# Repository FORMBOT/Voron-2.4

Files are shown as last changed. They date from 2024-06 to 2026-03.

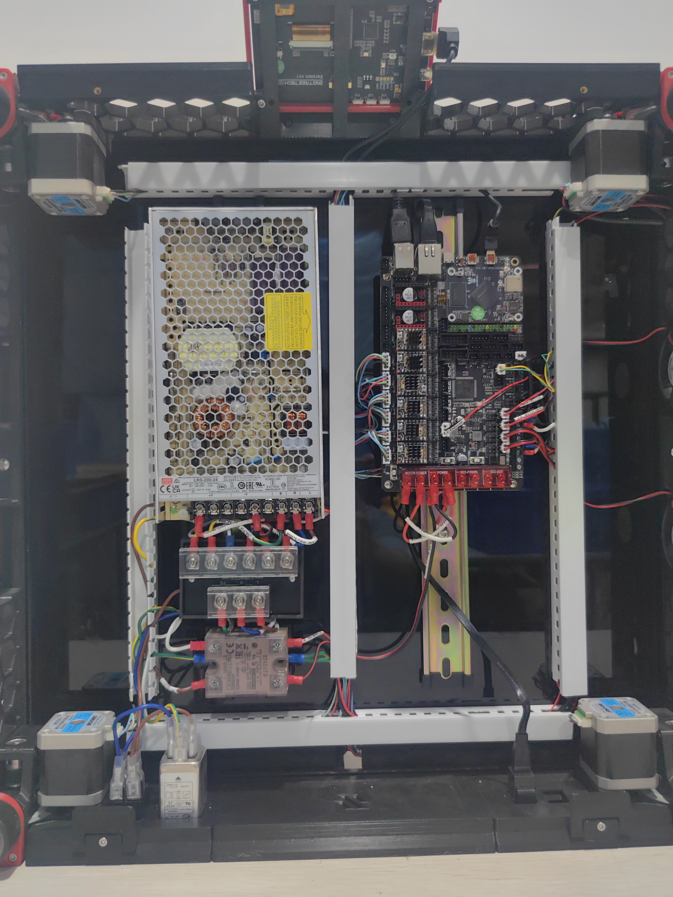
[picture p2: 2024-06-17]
Diagrams/Wiring Overview of V2.4 R2 Pro+.jpg

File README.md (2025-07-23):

# Voron V2.4 Formbot Kit

[Kit Website](https://www.formbot3d.com/products/voron-24-r2-pro-corexy-3d-printer-kit-with-m8p-cb1-board-and-canbus-wiring-system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)

# Overview

* [Build Notes](https://github.com/FORMBOT/Voron-2.4/tree/main/Build%20Notes)
* [Firmware Flashing](https://github.com/FORMBOT/Voron-2.4/tree/main/Firmware%20Flashing)
* [Config Setup and Initial Startup](https://github.com/FORMBOT/Voron-2.4/tree/main/Config)
* Maintenance
* [All STLs](https://github.com/FORMBOT/Voron-2.4/tree/main/STL)
* only custom STLs
* Printer Tuning
* Printer Testing

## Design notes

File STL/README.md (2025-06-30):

# Notes
STLs are tried to be kept up to date.
Original Repos: 
https://github.com/VoronDesign/Voron-2
https://github.com/VoronDesign/Voron-Stealthburner
https://github.com/VoronDesign/Voron-Tap
https://github.com/bigtreetech/EBB/tree/master/EBB%20SB2209%20CAN%20(RP2040)
https://github.com/nevermore3d/Nevermore_Micro/tree/master/V5_Duo
and some specific parts ;)

# Filename Nomenclature

| Filename | Note |
|---|---|
| \*.stl | Base color |
| [a]\_\*.stl | Accent color |
| [o]\_\*.stl | Opaque (light doesn't penetrate) |
| [c]\_\*.stl | Clear/Translucent (light can penetrate) |

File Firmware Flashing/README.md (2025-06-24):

# Firmware Flashing

First of all, be sure that your wiring is **100% correct** before you first power on your Printer. You should **disconnect* the bed heater and the SB2209 RP2040 completely, otherwise they may heat which could destroy your printed parts, hotend, bed heater, magnet sheet or thermal fuse.

## CB1/CB2 Setup
*this guide translates 1:1 to BTT Pi v1.1 / v2*
1. Get the [latest release of the cb1 firmware](https://github.com/bigtreetech/CB1/releases) (for cb2 get the [latest cb2 firmware release](https://github.com/bigtreetech/CB2/releases)). You want to download the XXX...XXX.img.xy file. This may take some time.
2. While you are waiting for the file to download, install the [Raspberry Pi Imager](https://www.raspberrypi.com/software/).
3. Unpack the firmware so you have a .img file.
4. Open the Raspberry Pi Imager, click on Choose OS, scroll down to the very end, klick on "Use Custom" and select the .img file you just unpacked.
5. Select the MicroSD card with the "Choose Storage" function.
6. Click on "WRITE" and accept that all previous data on the SD card will be deleted.
7. If the imager didn't already eject the SD-Card, eject it, pull it out from your Computer and plug it back in.
8. The Card will now show up as "BOOT".
9. Open the system.cfg file.
10. Remove the `#` in front of hostname and change it to whatever name you want your printer to show up in your network. E.g. `hostname="Voron"`
11. Remove the `#` in front of TimeZone and change it to your local time zone, E.g. `Europe/Munich`, `America/New_York` or `Asia/Shenzen`.
12. Go to WIFI_SSID and change it to your Wifi Name (`WIFI_SSID="YOURWIFINAME"`).
13. Go to WIFI_PASSWD and change it to your Wifi Password (`WIFI_PASSWD="YOURWIFIPASSWORD"`).
14. **DONT EDIT ANYTHING ELSE UNLESS YOU KNOW EXACTLY WHAT YOU ARE DOING!**

## CM4/5 Setup
*this guide translates 1:1 to Raspberry Pi 4 / 5*
1. Download and install [Raspberry Pi Imager](https://www.raspberrypi.com/software/).
2. Click “Choose OS” and scroll down to “Other specific-purpose OS”.
3. Select “3D Printing” and choose “Mainsail OS”.
4. Choose your SD Card.
5. If you will be using Wi-Fi, click on the GEAR icon in the bottom right corner and enter your Wi-Fi information.
6. Click on “SAVE” and on “WRITE”. and accept that all previous data on the SD card will be deleted.
7. Make sure that your MCU(s) is connected to your pi. If you will be using wired networking, also make sure your ethernet cable is connected.
8. Insert the microSD card into your Pi, and power on the Pi.
9. Find your Pi on the network, and ssh into it (using PuTTY on Windows or the terminal on MacOS). The default username is pi and the password is raspberry.
	* If your network supports bonjour, the pi should show up as mainsailos.local
	* If your network automatically assigns DNS hostnames, it may simply show up as mainsailos
	* Failing these two options, you may need to check your router’s DHCP server, and find out what IP address as been assigned to the device.

## CANBUS Setup
1. First of all, take a look at the [CANbus basics](https://canbus.esoterical.online).
2. Now [set up the CANbus Network](https://canbus.esoterical.online/Getting_Started.html).
3. [Flash your Mainboard](https://canbus.esoterical.online/mainboard_flashing.html). You need to flash it in USB-CAN-Bridge. You can find the needed Mainboard settings / hardware [here](https://canbus.esoterical.online/mainboard_flashing/common_hardware/BigTreeTech%20Manta%20M8P%20v2.0/README.html).
4. Now [flash your SB2209 RP2040](https://canbus.esoterical.online/toolhead_flashing.html). You can find the needed settings / hardware [here](https://canbus.esoterical.online/toolhead_flashing/common_hardware/BigTreeTech%20SB2209%20(RP2040)/README.html).
5. Note your UUIDs and note which one is the one of the Mainboard and which belongs to the toolhead.

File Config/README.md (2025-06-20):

# Configuration & Basic Macros

You still need to adjust a few things which are depending on your printer size!

Go through the config carefully. Everyone is responsible for their own configuration and for any damage that may occur due to incorrect configuration. "Uncomment" means remove the "#" in front of the line.

After you completed the first steps of your configuration, follow the [Voron Initial Startup Guide](https://docs.vorondesign.com/build/startup/) to set up everything else and be sure it works correct.
Follow [slicer setup](https://docs.vorondesign.com/build/slicer/) to set up your slicer.

Now that everything is set up, it's time for the [secondary Printer tuning](https://docs.vorondesign.com/tuning/secondary_printer_tuning.html) so your first print won't be a complete disaster.

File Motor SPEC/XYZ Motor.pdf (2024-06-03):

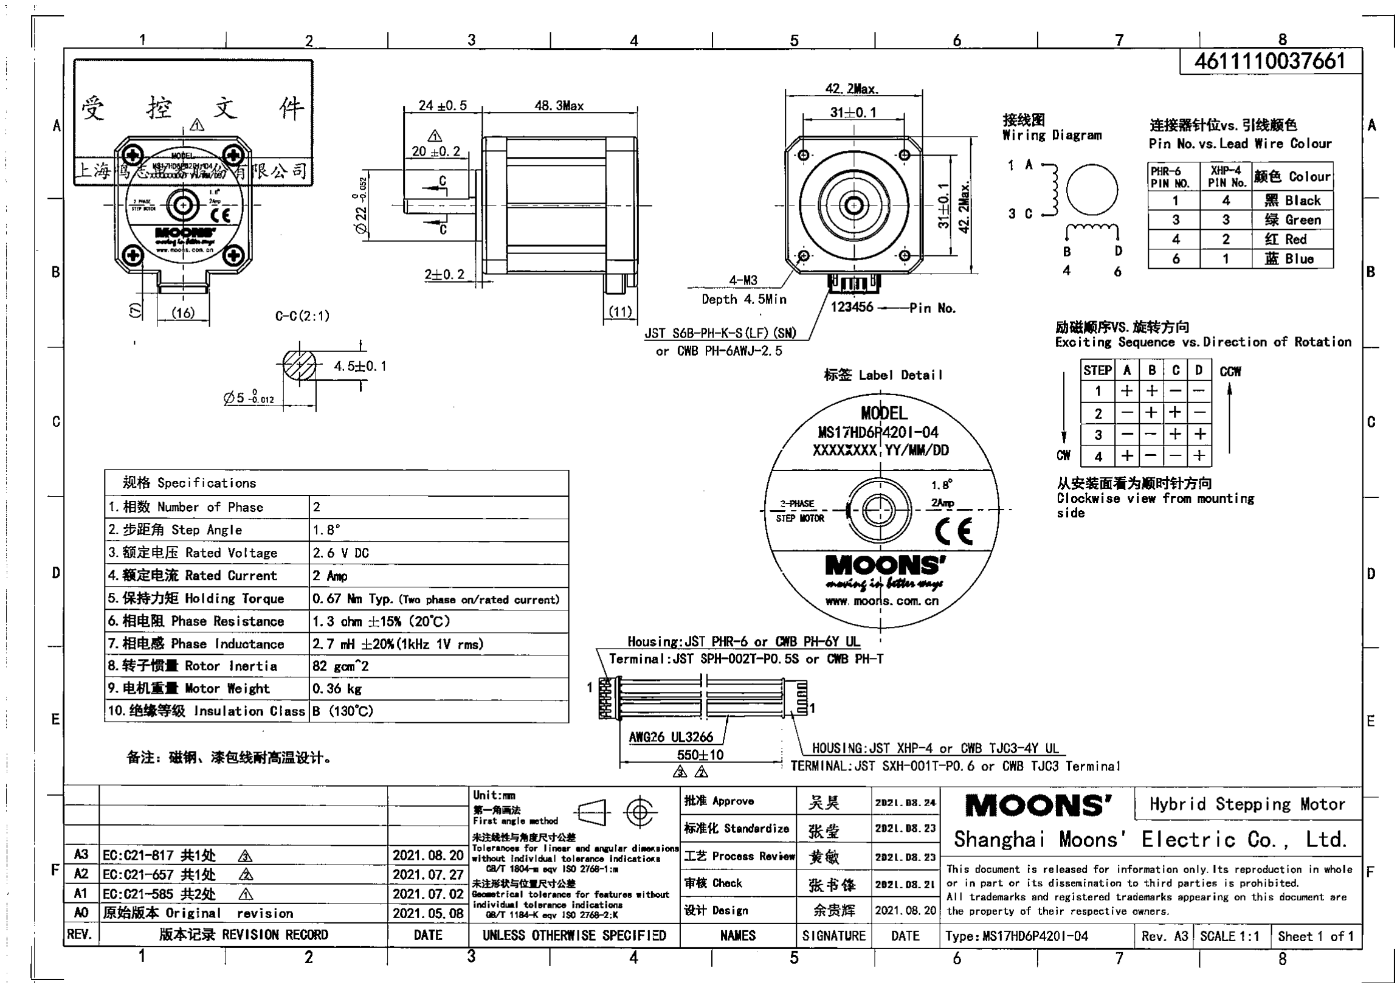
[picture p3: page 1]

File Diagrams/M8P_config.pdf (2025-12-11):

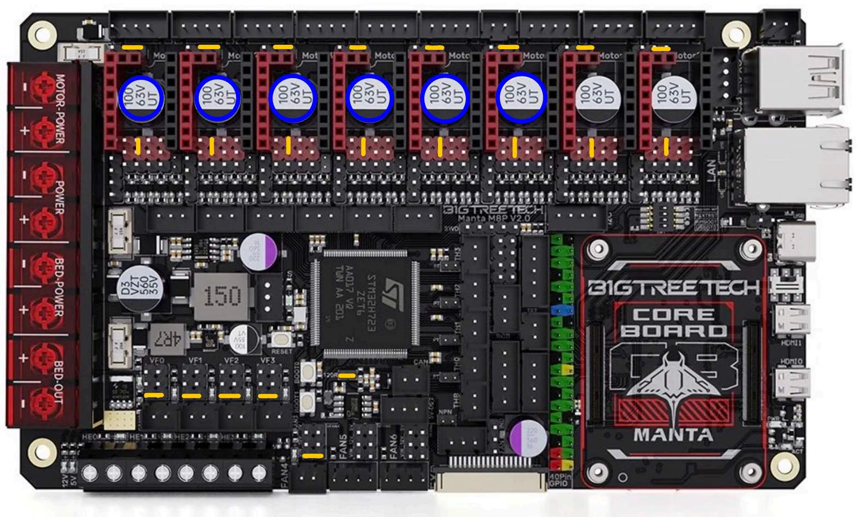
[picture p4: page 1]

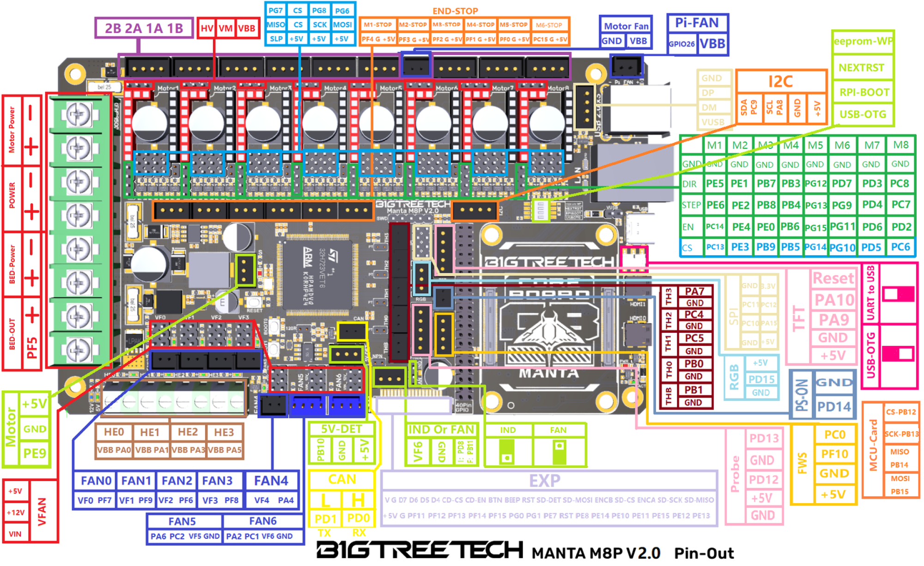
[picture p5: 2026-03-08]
Diagrams/Pins/BIGTREETECH MANTA M8P V2-0 PinOut.png

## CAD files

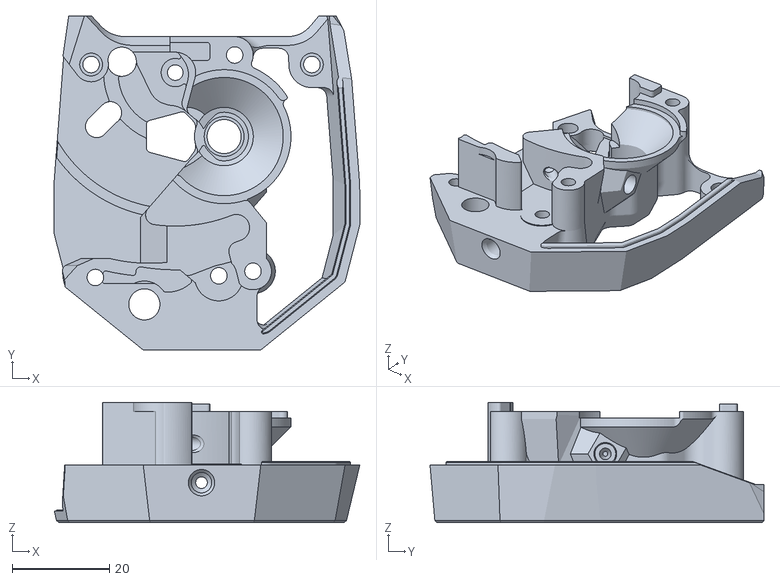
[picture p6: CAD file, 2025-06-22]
STL/Stealthburner/Clockwork2/Direct_Drive/main_body.stl
62.8 x 68.7 x 24.7

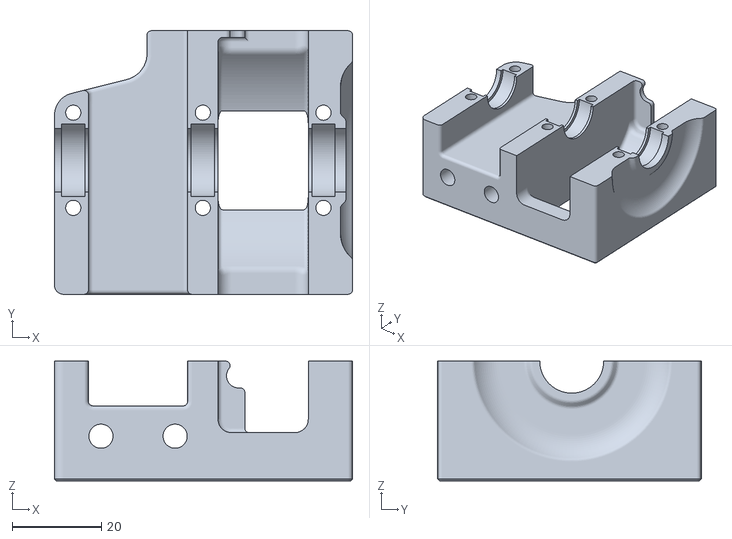
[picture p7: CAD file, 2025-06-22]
STL/Z_Drive/z_drive_main_a_x2.stl
66.7 x 59.0 x 26.8

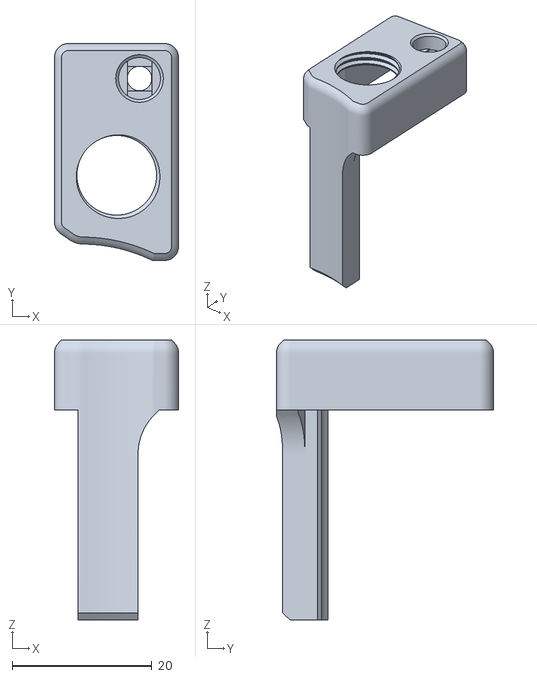
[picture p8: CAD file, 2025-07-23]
only custom STLs/Accent/PG7 Gantry Adapter.stl
17.7 x 31.0 x 40.0

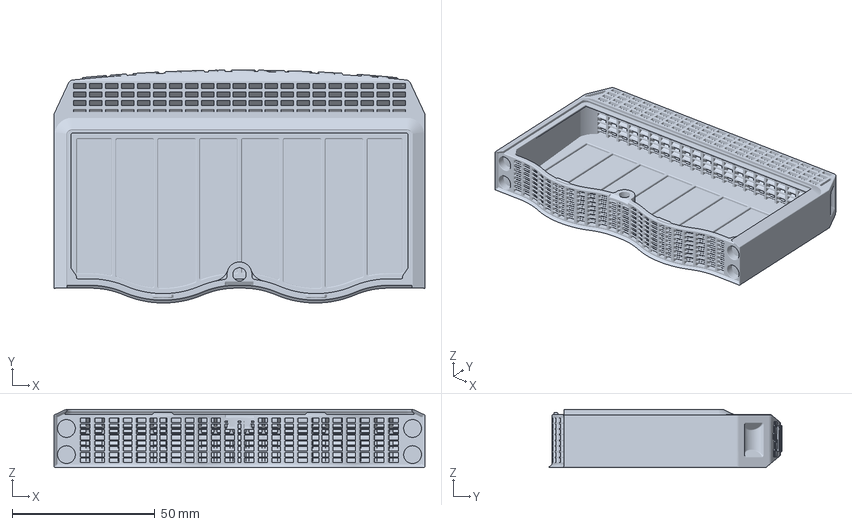
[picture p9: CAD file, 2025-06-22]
only custom STLs/Nevermore/XL_Cartridge(contributed_by_Bucknova).3mf
130.0 x 81.6 x 20.5 mm

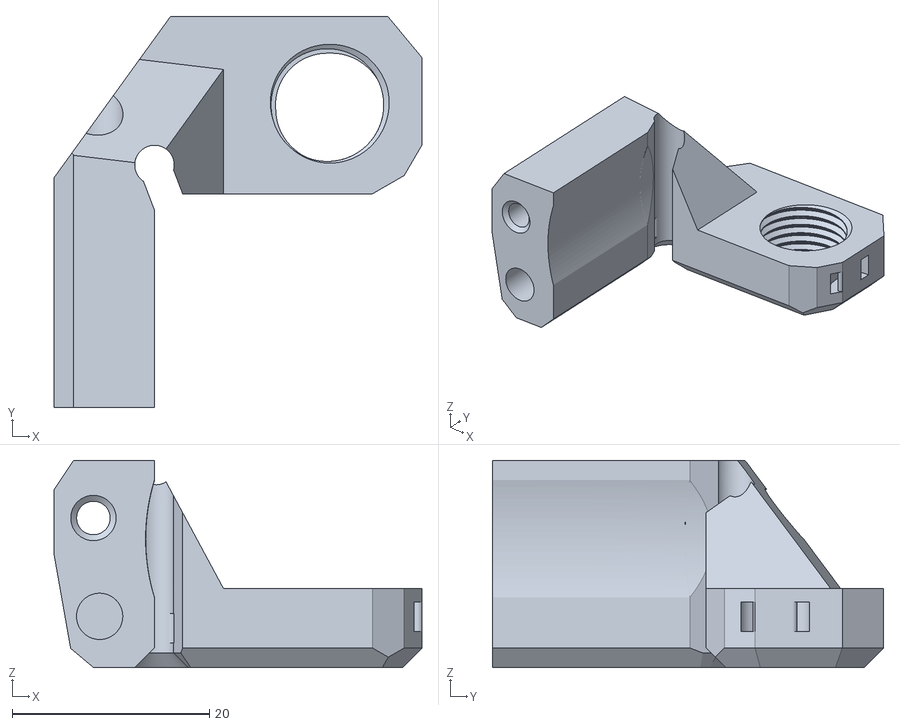
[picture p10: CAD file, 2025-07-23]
only custom STLs/Primary/Anchor v2.stl
37.3 x 39.7 x 21.1

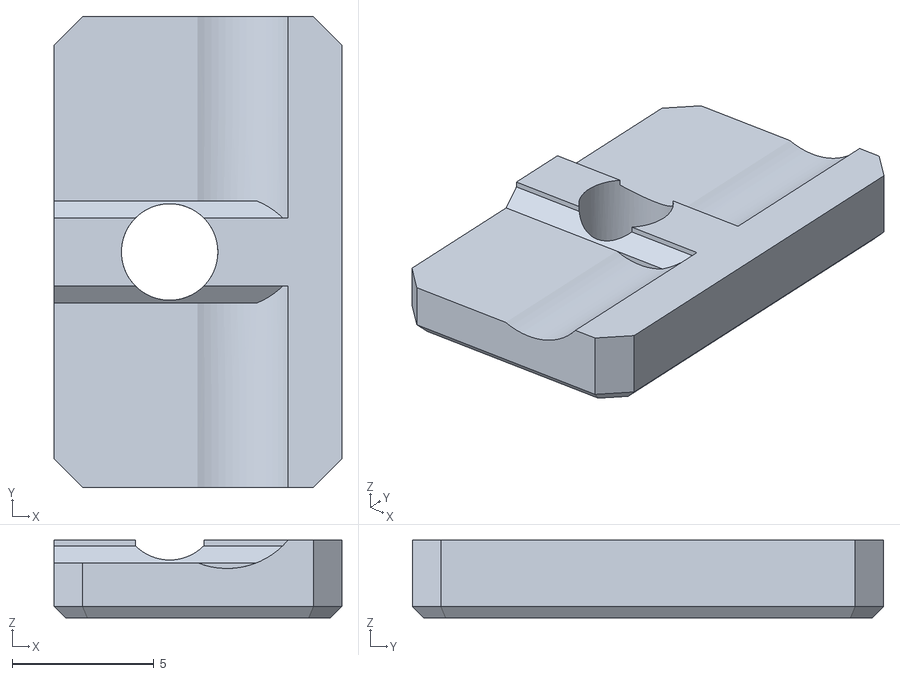
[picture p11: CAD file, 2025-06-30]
only custom STLs/Tap/[a]_Tap_Belt_Cover_r8_x2.stl
10.1 x 16.6 x 2.74

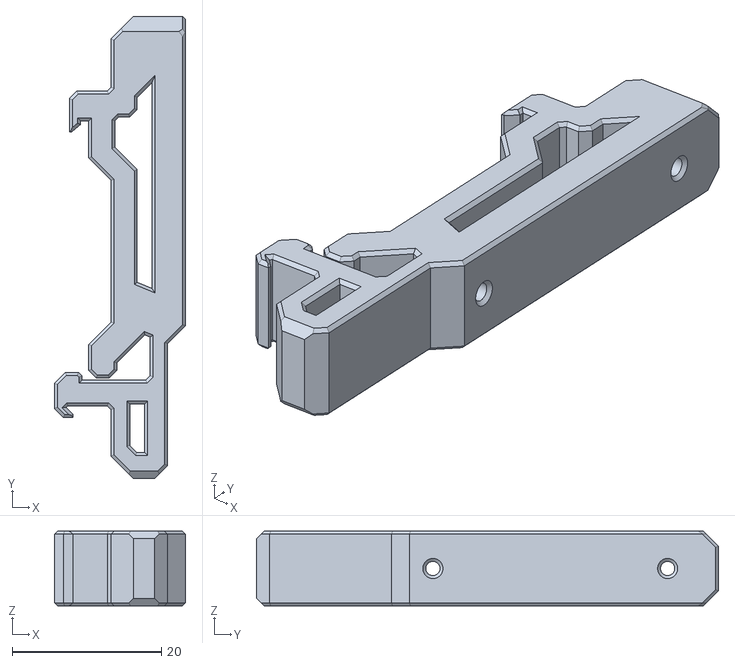
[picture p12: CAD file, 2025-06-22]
STL/Electronics_Bay/pcb_din_clip_x2.stl
17.6 x 62.0 x 10.0

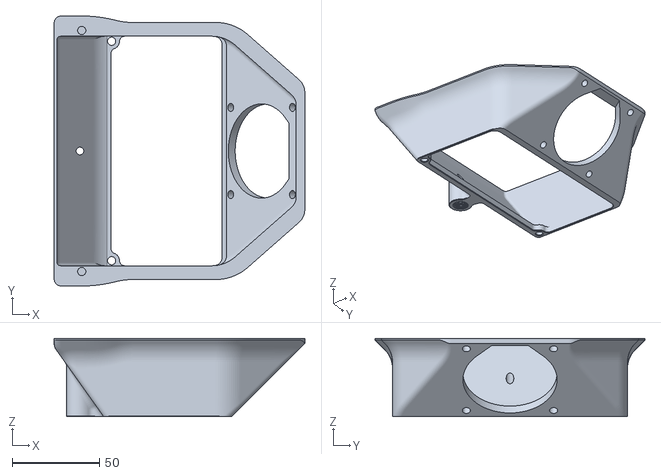
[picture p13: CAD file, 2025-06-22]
STL/Exhaust_Filter/exhaust_filter_housing.stl
143.7 x 154.8 x 45.0

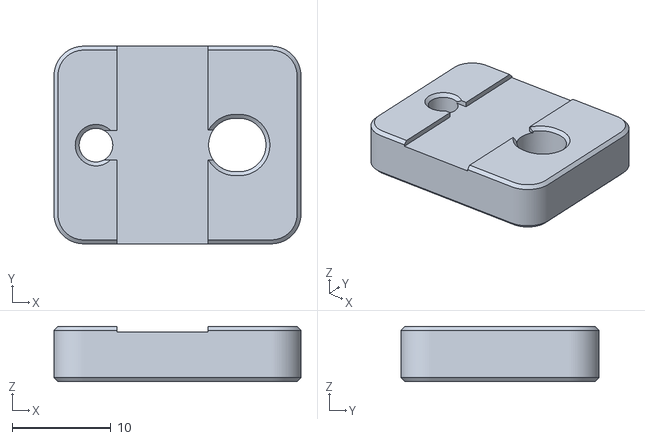
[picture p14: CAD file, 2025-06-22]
STL/Gantry/[a]_z_belt_clip_lower_x4.stl
25.0 x 20.0 x 5.60

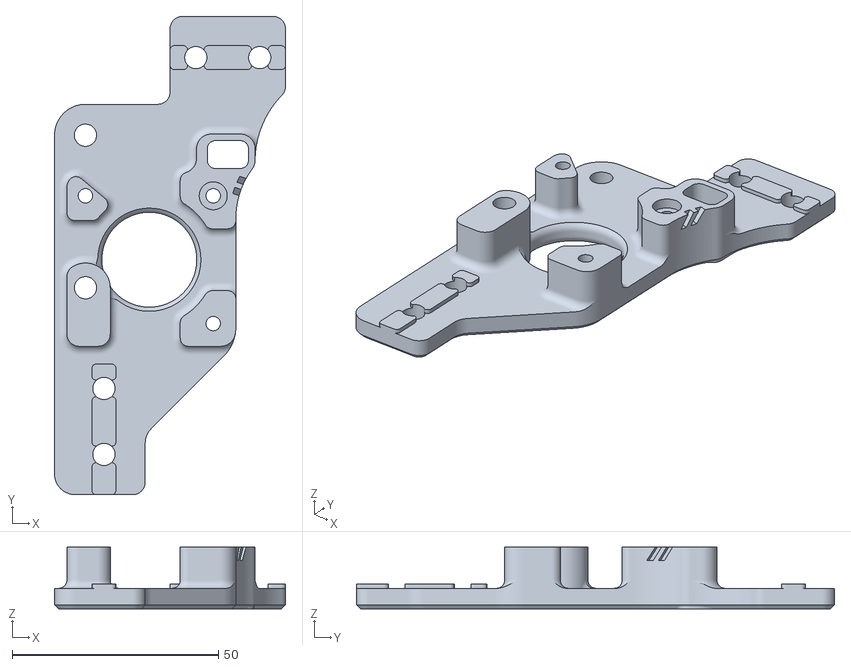
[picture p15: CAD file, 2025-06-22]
STL/Gantry/AB_Drive_Units/b_drive_frame_upper.stl
56.0 x 116.0 x 15.0

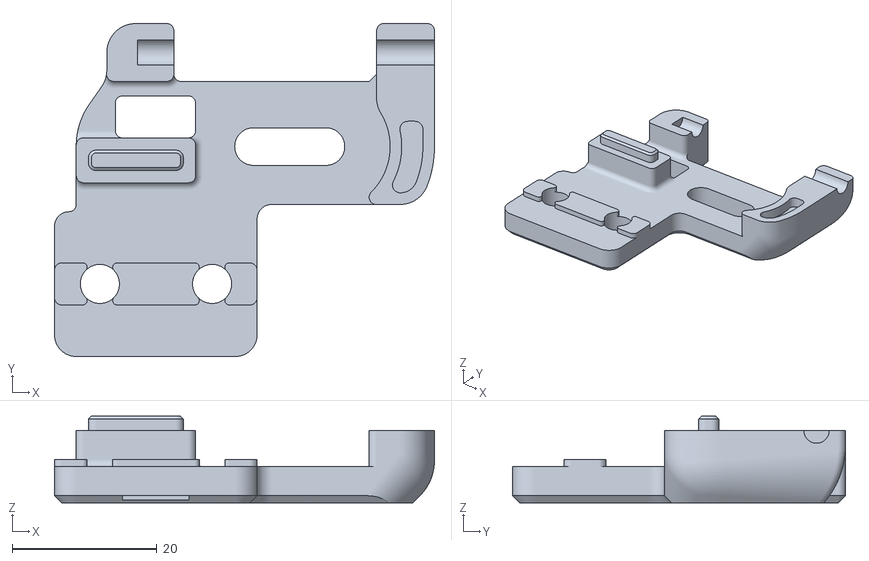
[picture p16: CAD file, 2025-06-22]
STL/Gantry/Front_Idlers/front_idler_right_upper.stl
52.5 x 46.0 x 12.0

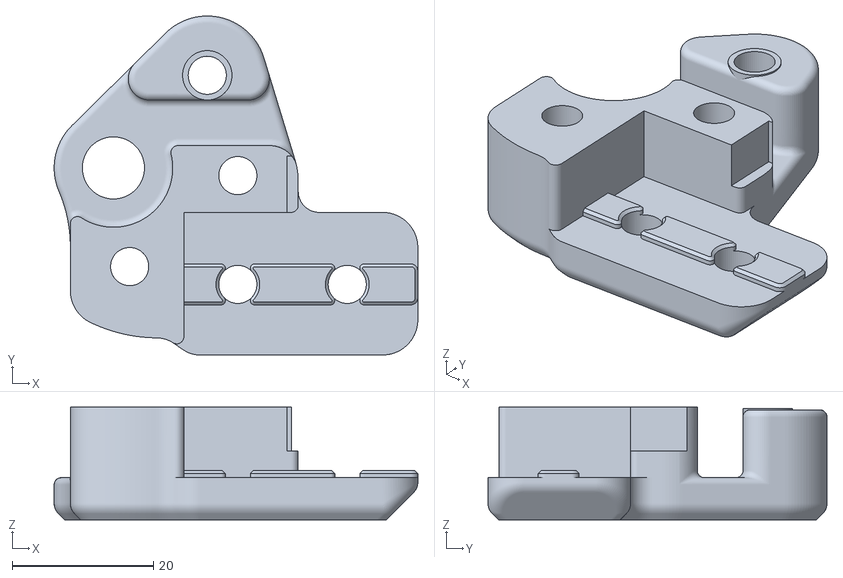
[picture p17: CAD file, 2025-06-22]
STL/Gantry/XY_Joints/xy_joint_left_upper_MGN12.stl
51.5 x 48.0 x 16.0

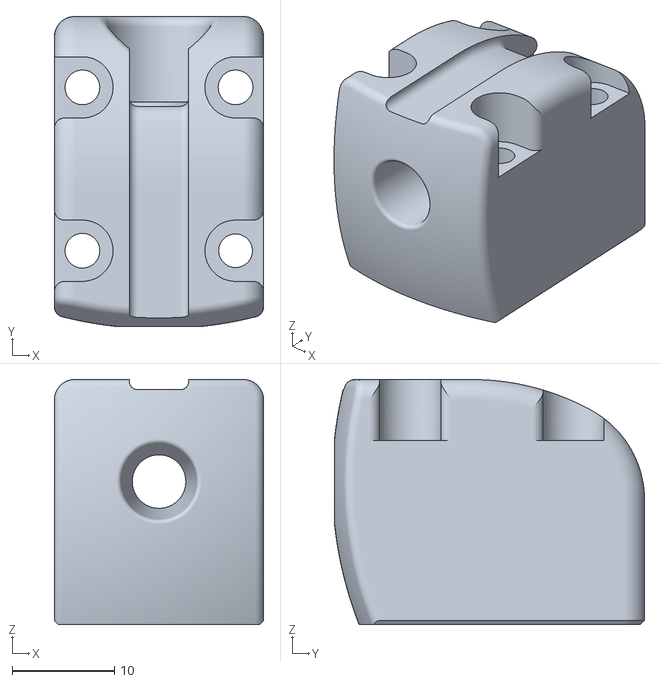
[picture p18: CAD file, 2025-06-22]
STL/Gantry/Z_Joints/z_joint_lower_x4.stl
20.5 x 30.4 x 24.0

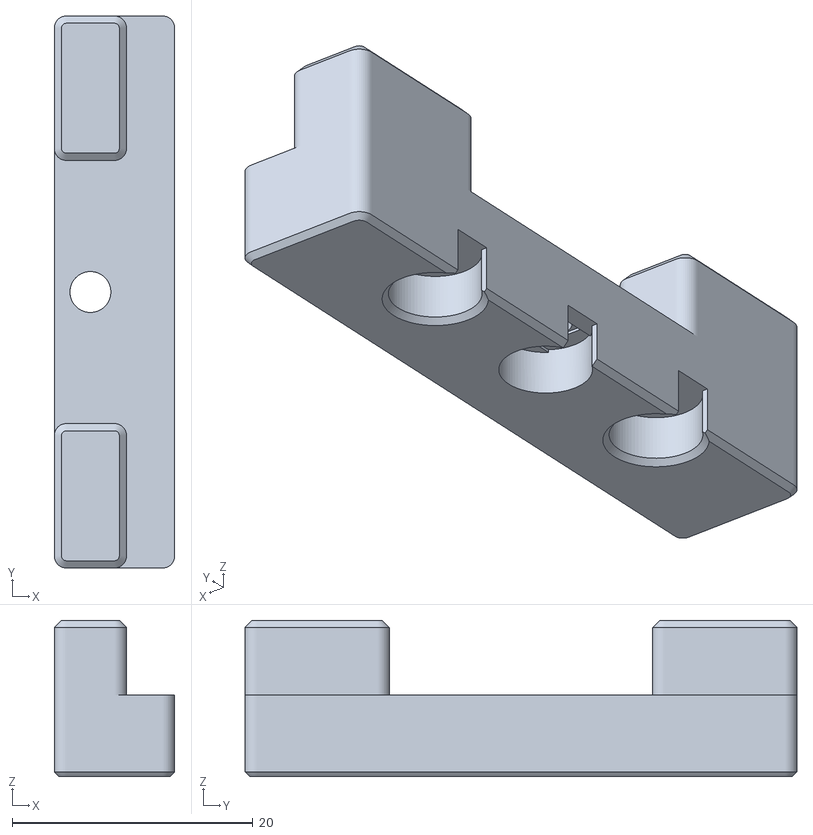
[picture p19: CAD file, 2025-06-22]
STL/Panel_Mounting/Front_Doors/latch_x2.stl
10.0 x 45.9 x 13.0

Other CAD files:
STL/Z_Drive/z_drive_main_b_x2.stl
STL/Panel_Mounting/midspan_panel_clip_6mm_x8.stl
STL/Skirts/250/front_skirt_a_250.stl
STL/Skirts/300/rear_center_skirt_300.stl
STL/Electronics_Bay/Manta-M8P_Bracket.stl
STL/Electronics_Bay/PSU_stabilizer_50mm.stl
STL/Electronics_Bay/lrs_200_psu_bracket_x2.stl
STL/Exhaust_Filter/[a]_exhaust_fan_grill.stl
STL/Exhaust_Filter/[a]_exhaust_filter_mount_x2.stl
STL/Exhaust_Filter/[a]_filter_access_cover.stl
STL/Exhaust_Filter/exhaust_filter_grill.stl
STL/Gantry/AB_Drive_Units/[a]_PG7-Umbilical Motor Mount.stl
STL/Gantry/AB_Drive_Units/[a]_z_chain_retainer_bracket_x2.stl
STL/Gantry/AB_Drive_Units/a_drive_frame_lower.stl
STL/Gantry/AB_Drive_Units/b_drive_frame_lower.stl
STL/Gantry/Front_Idlers/[a]_tensioner_left.stl
STL/Gantry/Front_Idlers/[a]_tensioner_right.stl
STL/Gantry/Front_Idlers/front_idler_left_lower.stl
STL/Gantry/Front_Idlers/front_idler_left_upper.stl
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

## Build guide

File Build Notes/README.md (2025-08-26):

# Functional parts build notes (to get the Printer up and running)
Start with the [Stock Voron 2.4 Manual](https://github.com/VoronDesign/Voron-2/tree/Voron2.4/Manual).
Be aware that the v2.4 Manual uses a 250mm Version of the v2, so some dimensions may seem wrong if you build a 300mm/350mm Version.

## P. 25 v2.4 manual: 
If you build a bigger Version than a 250mm, you need more screws / m3-T-Nuts. Start from the outer holes in the rail and work your way towards the middle screwing the rail down every second hole.
The carriages are designed to slide along the rail easily. This unfortunately also includes sliding off the rails. Dropping the carriage likely irreparably damages it. ALWAYS put the little black rubber Carriage stoppers back on the rail (into the holes without screws) until your printer ist up and runnning!

## P. 29 v2.4 manual:
The DIN-Rails need to be rotated 90 Degrees so the cables are long enough later. They should run parallel to the bed extrusions (from front to back).

## P. 84 v2.4 manual: 
Skip this step, this part is not used and therefore probably not included in your printed parts.

## P. 88 v2.4 manual: 
If you are building a 300mm machine you will need to start you screws from the second screw hole in the rails leaving the end holes open to allow space for T-nuts at later steps.
Small reminder: The carriages are designed to slide along the rail easily. This unfortunately also includes sliding off the rails. Dropping the carriage likely irreparably damages it. ALWAYS put the little black rubber Carriage stoppers back on the rail (into the holes without screws) until your printer ist up and runnning!

## P. 101 v2.4 manual: 
Again, if you are building a bigger printer than the 250mm version, start at the outer holes and screw the rail down every second hole.
Small reminder (again): The carriages are designed to slide along the rail easily. This unfortunately also includes sliding off the rails. Dropping the carriage likely irreparably damages it. ALWAYS put the little black rubber Carriage stoppers back on the rail (into the holes without screws) until your printer ist up and runnning!

## P. 104 v2.4 manual: 
As said before, the part on top of the right XY-Joint is not used with this kit. Use m5x10 BHCS like on the left XY-Joint to secure the X Axis to the XY-Joints.

## P. 122 v2.4 manual: 
After you installed the Z-belts and squared the Gantry, make sure your AB belts are exactly the same length and have the exact same amount of teeth! Proceed with routing the AB-Belts, but be Aware that you will use a different X carriage as in the Voron 2.4 Manual.

## P. 129-131 v2.4 manual: 
Skip these pages. Put the AB belts to the MGN12 Carriage with some tape, they dont have to be tight.

## P. 143 v2.4 manual: 
X Carriage: After finishing the AB-Belts Routing, switch to the [TAP Manual](https://github.com/VoronDesign/Voron-Tap/tree/main/Manual). Optotap is used as the sensor.
Be sure to take a look into the R8_errata.md document, it Highlights some important changes from the Manual and install the X Endstop switch.

## P. 33 Tap Manual: 
After you have installed Tap successfully and have the AB belts fixed in the tap carriage, switch to page 146 of the Voron 2.4 manual or to the [Stealthburner manual](https://github.com/VoronDesign/Voron-Stealthburner/tree/main/Manual).
We will come back to install the Toolhead later.

## P. 13 Stealthburner manual: 
You use a Toolhead PCB, so install these two heat inserts.

## P. 14 Stealthburner manual: 
Skip

## P. 30 Stealthburner manual: 
Follow [this Video Guide](https://www.youtube.com/watch?v=ly22qmB3NxE&t=1s) on how to set the gear mesh on your CW2.
Follow [this video Guide](https://www.youtube.com/watch?v=L1gxBCiE0pk) on how to set the Anti-Squish as well.

## P. 31 Stealthburner manual: 
Skip for now, we will install our Version of the Anchor later.

## P. 34 Stealthburner manual: 
You dont need to fix the Cable Cover down with the m3x6 BHCS now, you will need to access this later.

## P. 36-43 Stealthburner manual: 
All Hotends are mounted in a similar pattern and pretty self-explaining, your hotend mount and hotend will look different.

## P. 46-51 Stealthburner manual: 
Be very careful with the cables, you can easily rip them off the LED PCB which leads to this LED and the following ones not working.

## P. 53 Stealthburner manual: 
Be sure that your fan blows in the right Direction. Look at the arrows on the fan. Additionally, the Sticker on the fan is on the back pointing towards the Hotend. You want the fan to blow air into the hotend, not trying to pull the air out. This destroys your fan and your whole hotend mount because of heatcreep.

## P. 56 Stealthburner manual: 
You dont need to screw the 5015 fan into the SB Face, you will install the SB0000 Fan PCB there later.

## P. 58 Stealthburner manual: 
All parts of the Stealthburner are now pretty much finished. Now you will need to install the Can-Board on there and do some basic wiring. Switch to the [SB2209 RP2040 Manual](https://github.com/bigtreetech/EBB/tree/master/EBB%20SB2209%20CAN%20(RP2040)/Build%20Guide).

## P. 02 SB2209 manual: 
Now you need to screw down the 5015 fan with the SB0000 PCB :)

## P. 03/04 SB2209 manual: 
You need to select Vin (24V) for all fans. Be sure to wire Gnd to Gnd and 24V to 24V! Otherwise you will experience magic smoke later.

## P. 05 SB2209 manual: 
Skip

## P. 06 SB2209 manual: 
Be sure to wire Gnd to Gnd, Signal to Signal and 24V to 24V! Otherwise you will experience magic smoke later.

## P. 13 SB2209 manual: 
You Need to set the switch to 1: on; 2: on; 3: off; 4: on

## P. 15 SB2209 manual: 
Skip

## P. 16 SB2209 manual:
Be sure to use the endstop labeled "To CAN_Endstop" which is the one with the short wires.

## P. 18 SB2209 manual: 
Skip

## P. 19 SB2209 manual: 
Skip, Stealthburner will be assembled later.

## P. 24 SB2209 manual: 
You will need to Strip down the Isolation a bit so you have enough cable length to connect the cable to the PSU and to the Can port. Go back to the Tap Manual page 34 now, flashing the toolhead will be done later.
Use the tight cable sleeve around the cable.

## P. 36 Tap manual: 
Stealthburner and Tap are now completed and installed. Switch back to p. 148 of the original V2.4 manual.

## P. 149 v2.4 manual:
Rotate the din rails 90° compared to the original layout.

## P. 150-152 v2.4 manual: 
Skip; Raspberry Pi mounting and 5v PSU mounting is not needed. Instead, mount the CB1 / CM4 on the Manta.

## P.158-164 v2.4 manual:
Skip; TAP is your Z-Endstop, your X Endstop sits on Tap and your Y endstop will be mounted on the A Motor mount later.

## P. 165 v2.4 manual: 
You use the 3in6 Power Distributor instead.

## P. 170 v2.4 manual:
small reminder, you dont use a Raspberry Pi.

## P. 172 v2.4 manual:
another small reminder, you don't use a 5v PSU.

## P. 175-178 v2.4 manual:
Skip these steps, instead configure your Manta like this:
M8P_v2 Jumper / Driver marking
Place a Jumper on all yellow marked pins and place the TMC2209s with attached heatsink on all driver ports with a blue circle after installing the jumpers.

## P. 183 v2.4 manual: 
Leave the cables to the 5v PSU out.

## P. 184 v2.4 manual:
The Z-Endstop cables are not needed.

## P. 185 v2.4 manual: 
Be **100%** sure that the SSR cables are connected correctly, **otherwise your printer is _not_ safe to be powered on**.

## P. 186-189 v2.4 manual:
This kit doesn't use Wagos to distribute the High Voltage cables.

## P. 190-193 v2.4 manual: 
These steps are for an octopus Mainboard. Use this wiring diagram instead: v2.4 M8P wiring diagram
For now, only connect z0-z3, the bed heater, 24V from the 24V PSU and the bed thermistor.

## P. 194-199 v2.4 manual:
Skip these steps, you use Umbilical on X and Y.

## P. 204 v2.4 manual:
You use a bit different Wire guide where you have to screw in a pg7 cable gland. From here you route the Can cable down through the z chain, together with the A and B Motor cables. 
v2.4 M8P wiring diagram 
Connect the B motor (left motor) to X Motor, connect the A motor (right motor) to Y Motor.
Connect the CAN-Cable to the right CAN-Port on the M8P and 24V / GND to the 24V PSU. If you think the cables are not Long enough, you haven't done [this step](https://github.com/FORMBOT/Voron-2.4/tree/main/Build%20Notes#p-24-sb2209-manual).

# Cosmetic parts build notes (not needed to get the pinter running)

## P. 206-209 v2.4 manual:
You can skip these steps.

## P. 211 & 214-216 & 220-221 v2.4 manual:
Skip; you don't need these parts because you use the touchscreen.

## P. 231 v2.4 manual:
Use the v2.4 M8P wiring diagram to wire the electronics fans.

## P. 233 v2.4 manual: 
Don't close the electronics compartment yet, you will need to acces this while flashing the boards.

## P. 256 v2.4 manual:
Use the big cable sleeve around the exhaust fan cable (if you use the stock exhaust).

# Don't power on the printer if you are not 100% sure you wired everything correct!
And have a look into [this](https://github.com/FORMBOT/Voron-2.4/blob/main/Diagrams/Instruction%20of%20V2.4%20R2%20Pro%2B.pdf).

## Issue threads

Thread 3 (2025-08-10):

published config has broken [resonance_tester] block

shiftingtech, 2025-08-10:
published config contains a [resonance_tester] block ,but not the required `accelerometer` line  (plus the entire [adxl3465] block is missing), resulting in a nonfunctional config.

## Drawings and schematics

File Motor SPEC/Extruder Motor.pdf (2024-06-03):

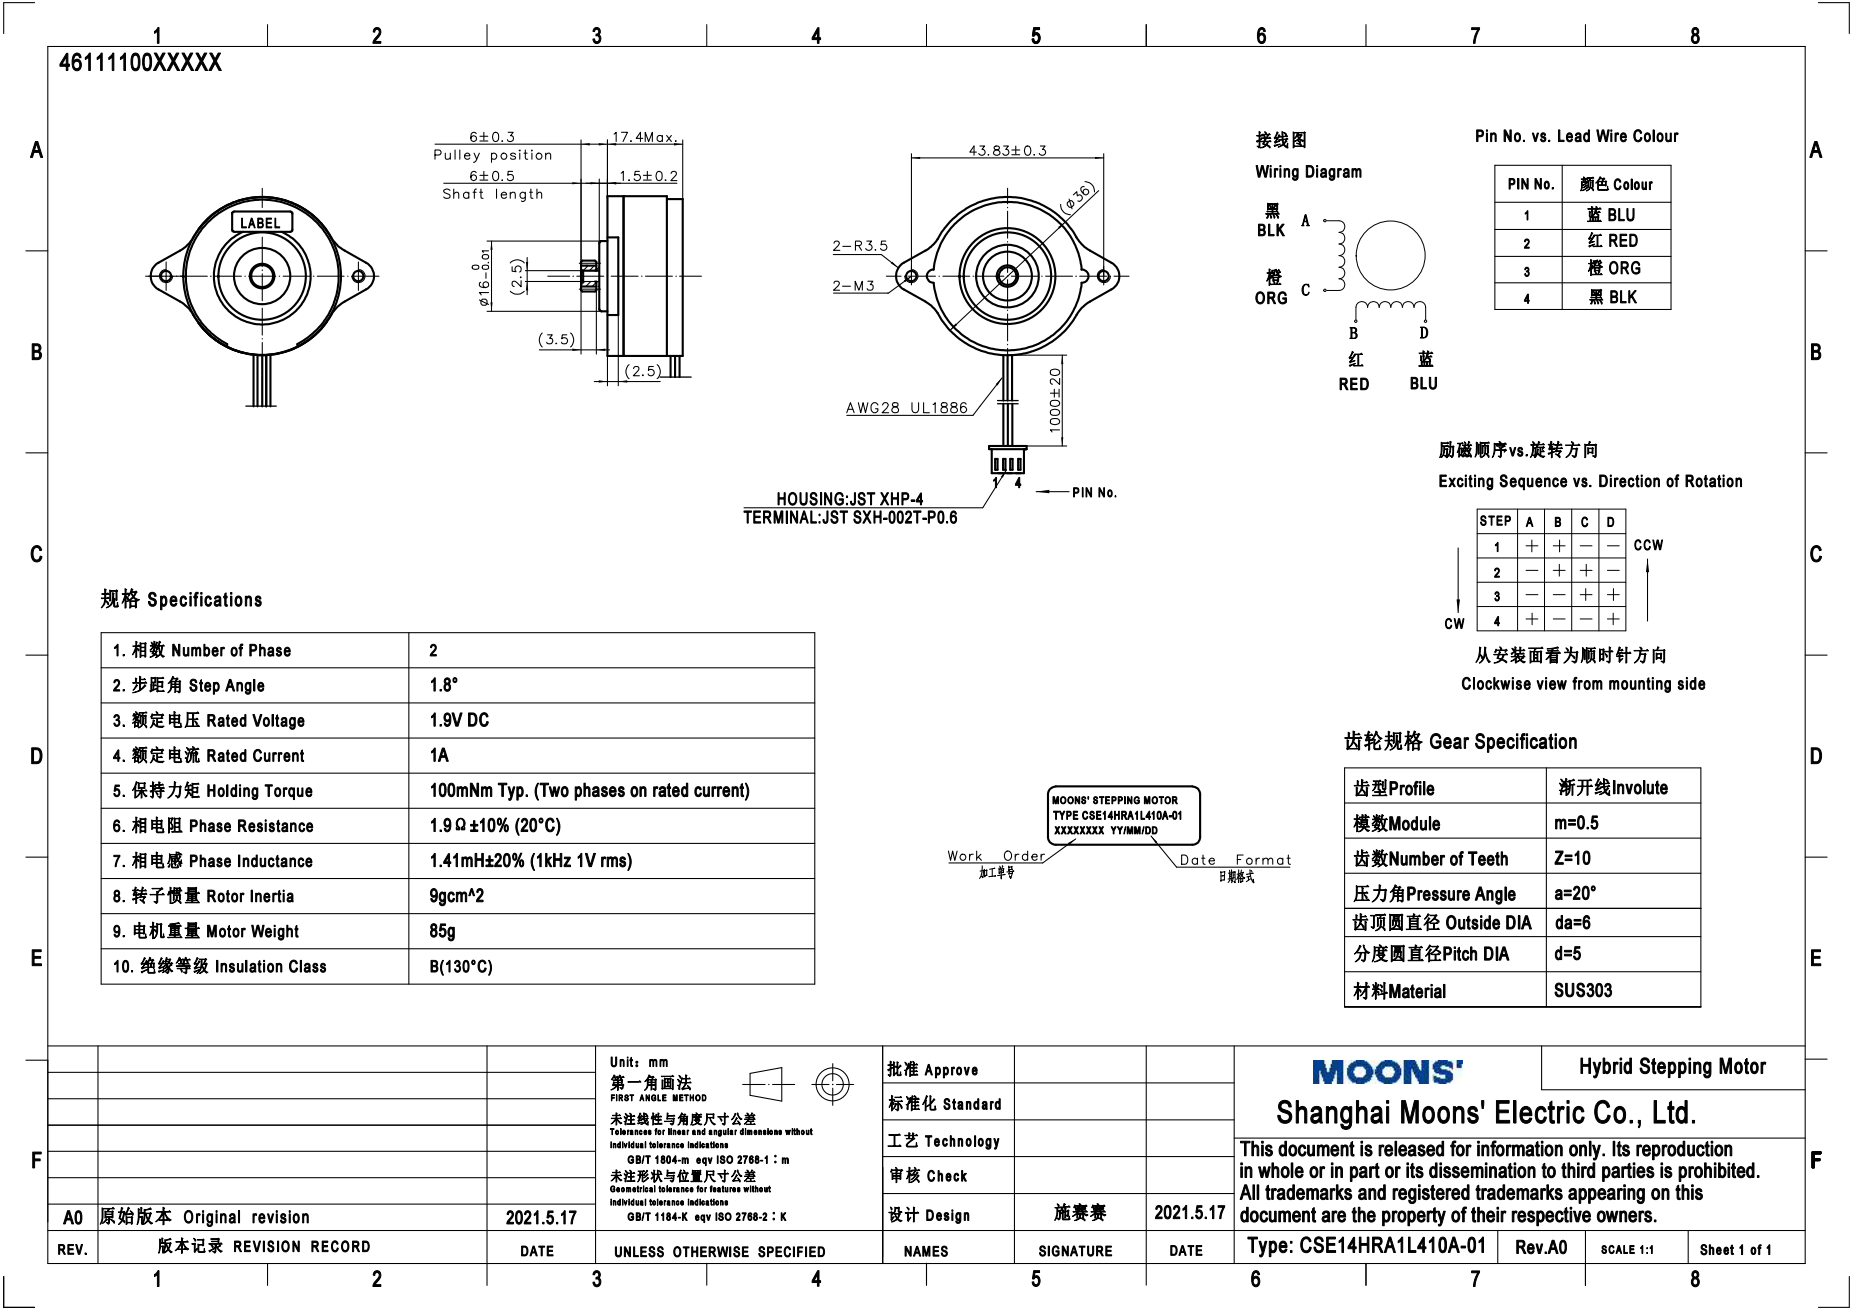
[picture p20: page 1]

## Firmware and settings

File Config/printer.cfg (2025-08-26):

[mcu]
canbus_uuid: YOU_DIDNT_CHANGE_ME_YET						# Insert the CANbus-UUID of your Manta from the firmware flashing steps

[mcu EBBCan]
canbus_uuid: YOU_DIDNT_CHANGE_ME_YET						# Insert the CANbus-UUID of your SB2209 RP2040 from the firmware flashing steps

[printer]
kinematics: corexy
max_velocity: 300  
max_accel: 10000    			
max_z_velocity: 30 			
max_z_accel: 350
square_corner_velocity: 5.0

[temperature_sensor MCU]
sensor_type: temperature_mcu

[temperature_sensor SoC]
sensor_type: temperature_host

#####################################################################
# 	X/Y Stepper Settings
#####################################################################

## X Stepper on Motor1 (B Motor)
[stepper_x]
step_pin: PE6
dir_pin: PE5
enable_pin: !PC14
microsteps: 16
rotation_distance: 40
full_steps_per_rotation:200  #set to 400 for 0.9 degree stepper
endstop_pin: ^EBBCan:gpio24
position_min: 0
##--------------------------------------------------------------------

##	Uncomment below for 250mm build
#position_endstop: 250
#position_max: 250

##	Uncomment for 300mm build
#position_endstop: 300
#position_max: 300

##	Uncomment for 350mm build
#position_endstop: 350
#position_max: 350

##--------------------------------------------------------------------
homing_speed: 25
homing_retract_dist: 5
homing_positive_dir: true


[tmc2209 stepper_x]
uart_pin: PC13
interpolate: True
run_current: 0.9
sense_resistor: 0.110
stealthchop_threshold: 0

## Y Stepper on Motor2 (A Motor)
[stepper_y]
step_pin: PE2
dir_pin: PE1
enable_pin: !PE4
microsteps: 16
rotation_distance: 40
endstop_pin: ^PF3
full_steps_per_rotation:200  #set to 400 for 0.9 degree stepper
position_min: 0
##--------------------------------------------------------------------

##	Uncomment for 250mm build
#position_endstop: 250
#position_max: 250

##	Uncomment for 300mm build
#position_endstop: 300
#position_max: 300

##	Uncomment for 350mm build
#position_endstop: 350
#position_max: 350

##--------------------------------------------------------------------
homing_speed: 25
homing_retract_dist: 5
homing_positive_dir: true


[tmc2209 stepper_y]
uart_pin: PE3
interpolate: True
run_current: 0.9
sense_resistor: 0.110
stealthchop_threshold: 0


#####################################################################
# 	Z Stepper Settings
#####################################################################

## Z0 Stepper - Front Left on MOTOR3_A
[stepper_z]
step_pin: PB8
dir_pin: PB7
enable_pin: !PE0
rotation_distance: 40
gear_ratio: 80:16
microsteps: 16
endstop_pin: probe:z_virtual_endstop
##--------------------------------------------------------------------

##	Uncomment below for 250mm build
#position_max: 240

##	Uncomment below for 300mm build
#position_max: 290

##	Uncomment below for 350mm build
#position_max: 340

##--------------------------------------------------------------------
position_min: -5
homing_speed: 8
second_homing_speed: 3
homing_retract_dist: 3


[tmc2209 stepper_z]
uart_pin: PB9
interpolate: true
run_current: 0.8
sense_resistor: 0.110
stealthchop_threshold: 0

##	Z1 Stepper - Rear Left on Motor5
[stepper_z1]
step_pin: PB4
dir_pin: !PB3
enable_pin: !PB6
rotation_distance: 40
gear_ratio: 80:16
microsteps: 16


[tmc2209 stepper_z1]
uart_pin: PB5
interpolate: true
run_current: 0.8
sense_resistor: 0.110
stealthchop_threshold: 0

##	Z2 Stepper - Rear Right on Motor6
[stepper_z2]
step_pin: PG13
dir_pin: PG12
enable_pin: !PG15
rotation_distance: 40
gear_ratio: 80:16
microsteps: 16


[tmc2209 stepper_z2]
uart_pin: PG14
interpolate: true
run_current: 0.8
sense_resistor: 0.110
stealthchop_threshold: 0

##	Z3 Stepper - Front Right on Motor7
[stepper_z3]
step_pin: PG9
dir_pin: !PD7
enable_pin: !PG11
rotation_distance: 40
gear_ratio: 80:16
microsteps: 16


[tmc2209 stepper_z3]
uart_pin: PG10
interpolate: true
run_current: 0.8
sense_resistor: 0.110
stealthchop_threshold: 0

#####################################################################
# 	Extruder
#####################################################################

#	E0 on SB2209
[extruder]
step_pin: EBBCan:gpio18
dir_pin: EBBCan:gpio19
enable_pin: !EBBCan:gpio17
microsteps: 16
rotation_distance: 22.905740611
gear_ratio: 50:10
nozzle_diameter: 0.400
filament_diameter: 1.750
heater_pin: EBBCan:gpio7
control: pid
min_temp: 0
max_extrude_only_distance: 105
max_extrude_cross_section: 2
pid_kp: 57.369
pid_ki: 2.533
pid_kd: 324.854
sensor_type: MAX31865
sensor_pin: EBBCan:gpio9
spi_software_sclk_pin: EBBCan:gpio10
spi_software_mosi_pin: EBBCan:gpio8
spi_software_miso_pin: EBBCan:gpio11
rtd_nominal_r: 100
rtd_reference_r: 430
rtd_num_of_wires: 2

[tmc2209 extruder]
uart_pin: EBBCan:gpio20
run_current: 0.65
stealthchop_threshold: 0


#####################################################################
# 	Bed Heater
#####################################################################

[heater_bed]
heater_pin: PA1
sensor_type: Generic 3950
sensor_pin: PB1
max_power: 1.0
min_temp: 0
max_temp: 115
control: pid
pid_kp: 58.437
pid_ki: 2.347
pid_kd: 363.769


#####################################################################
# 	Probe
#####################################################################

[probe]
pin: ^EBBCan:gpio22
x_offset: 0
y_offset: 0
#z_offset: 0
lift_speed: 30
activate_gcode:
    {% set PROBE_TEMP = 150 %}
    {% set MAX_TEMP = PROBE_TEMP + 5 %}
    {% set ACTUAL_TEMP = printer.extruder.temperature %}
    {% set TARGET_TEMP = printer.extruder.target %}

    {% if TARGET_TEMP > PROBE_TEMP %}
        { action_respond_info('Extruder temperature target of %.1fC is too high, lowering to %.1fC' % (TARGET_TEMP, PROBE_TEMP)) }
        M109 S{ PROBE_TEMP }
    {% else %}
        # Temperature target is already low enough, but nozzle may still be too hot.
        {% if ACTUAL_TEMP > MAX_TEMP %}
            { action_respond_info('Extruder temperature %.1fC is still too high, waiting until below %.1fC' % (ACTUAL_TEMP, MAX_TEMP)) }
            TEMPERATURE_WAIT SENSOR=extruder MAXIMUM={ MAX_TEMP }
        {% endif %}
    {% endif %}

#####################################################################
# 	Fan Control
#####################################################################

[fan]
pin: EBBCan:gpio13

[heater_fan hotend_fan]
pin: EBBCan:gpio14
heater: extruder
heater_temp: 70.0


[fan_generic nevermore]
##	Print Cooling Fan - CNC_FAN0
pin: PF8
kick_start_time: 0.5
off_below: 0.10

[controller_fan controller_fan_1]
##	Hotend Fan - CNC_FAN1
pin: PF9
max_power: 1.0
kick_start_time: 0.5
fan_speed: 0.66


[heater_fan controller_fan_2]
##	Controller fan - CNC_FAN2
pin: PF6
kick_start_time: 0.5
heater: heater_bed
heater_temp: 80
fan_speed: 0.66

[fan_generic exhaust_fan]
#	Exhaust fan - CNC_FAN0
pin: PF7
max_power: 1.0
shutdown_speed: 0.0
kick_start_time: 0.5

#####################################################################
# 	LED Control
#####################################################################

[neopixel toolhead_light]
pin: EBBCan:gpio16
chain_count: 3
color_order: GRBW

[output_pin caselight]
#Chamber Lighting - HE3 Connector
pin: PA3
pwm:true
shutdown_value: 0
cycle_time: 0.01

#####################################################################
# 	Homing and Gantry Adjustment Routines
#####################################################################

[idle_timeout]
timeout: 3300

[safe_z_home]
##--------------------------------------------------------------------

##	Uncomment below for 250mm build
#home_xy_position: 125,125

##	Uncomment below for 300mm build
#home_xy_position: 150,150

##	Uncomment below for 350mm build
#home_xy_position: 175,175

##--------------------------------------------------------------------
speed: 100
z_hop: 10

[quad_gantry_level]
##	Use QUAD_GANTRY_LEVEL to level a gantry.
##	Min & Max gantry corners - measure from nozzle at MIN (0,0) and 
##	MAX (250, 250), (300,300), or (350,350) depending on your printer size
##	to respective belt positions

#--------------------------------------------------------------------
##	Gantry Corners for 250mm Build
##	Uncomment for 250mm build
#gantry_corners:
#	-60,-10
#	310, 320
##	Probe points
#points:
#	50,25
#	50,175
#	200,175
#	200,25
	
##	Gantry Corners for 300mm Build
##	Uncomment for 300mm build
#gantry_corners:
#	-60,-10
#	360,370
##	Probe points
#points:
#	50,25
#	50,225
#	250,225
#	250,25

##	Gantry Corners for 350mm Build
##	Uncomment for 350mm build
gantry_corners:
	-60,-10
	410,420
#	Probe points
points:
	50,25
	50,275
	300,275
	300,25

#--------------------------------------------------------------------
speed: 100
horizontal_move_z: 10
retries: 10
retry_tolerance: 0.0075
max_adjust: 10

[bed_mesh]
mesh_min: 10,10
##--------------------------------------------------------------------

##	Uncomment below for 250mm build
#mesh_max: 240,240

##	Uncomment below for 300mm build
mesh_max: 290,290


##	Uncomment below for 350mm build
#mesh_max: 340,340
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

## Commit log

2024-05-24 Create STL Files of Voron 2.4 R2 Pro+
2024-05-24 Update STL Files of Voron 2.4 R2 Pro+
2024-05-31 ADD STL and cleanup
    [CW2 Cable Bridge.STL, Duo_Plenum_Lid.stl, Duo_Plenum_wago.stl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]
2024-06-03 Create Motor SPEC
2024-06-03 Create Extruder Motor
2024-07-12 Rename HDMI5 Screen Holder.stl to HDMI5 V1.1 Screen Holder.stl
    [HDMI5 Screen Holder.stl, HDMI5 V1.1 Screen Holder.stl]
2024-12-29 fix naming
    [3-6.STL, Manta_M8P_2pc.stl]
2024-12-30 Delete STL/Accent/HDMI5 V1.1 Screen Holder.stl
    REMOVE BROKEN FILE
    [HDMI5 V1.1 Screen Holder.stl]
2025-06-20 Din Rail rotation
2025-06-20 Example Config
    [Voron2_M8P-v2.0_config.cfg]
2025-06-20 bed mesh
    [printer.cfg]
2025-06-20 Secondary printer tuning
2025-06-22 added which endstop to use on toolhead
2025-06-22 All STLs
    [3_6.stl, Duo_Plenum_Lid.stl, Duo_Plenum_wago.stl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]
2025-06-30 Tap STLs
    [Tap_Center_left_r8.stl, Tap_Center_right_r8.stl, Tap_Front_r8.stl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]
2025-07-23 only custom stls as new folder
    [3-6.STL, Anchor v2.stl, BTT HDMI5 V1_2 mount bracket_Regular.stl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]
2025-08-26 Pin fix Z1/2/3 + Caselight
    [printer.cfg]
2025-08-26 Pin change
    [printer.cfg]
